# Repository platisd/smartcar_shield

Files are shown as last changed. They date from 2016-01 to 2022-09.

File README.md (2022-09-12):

# Smartcar shield








A versatile and easy to use vehicle platform for hobby-grade projects

- [Description](#description)
- [Hardware](#hardware)
- [Software](#software)
- [Reference platforms](#reference-platforms)
- [How to get started](#how-to-get-started)
- [Dependencies](#dependencies)
- [Project documentation](#project-documentation)
- [License](#license)

## Description
This repository, includes everything necessary to set up a Smartcar platform.
The Smartcar, is a vehicular educational platform, which enables the user to develop
various robotic applications in an affordable, pedagogic and easy way. It is intended
for persons with basic programming knowledge and little to no experience of electronics,
mechanics or robotics. More experienced users, should also find this approach convenient,
due to its open source nature, high level API and object oriented design.

## Hardware
Despite the software being hardware-agnostic, historically, development has been based on specific
hardware. Initially, the **Smartcar shield** was used on top of an Arduino, using cheap car kits.
This setup will be referred to as `shield` or `v1`.

Since the winter of 2019, a new platform was developed from scratch, using the WiFi and Bluetooth
enabled ESP32 as the vehicle's "brain". This setup will be referred to as `platform` or `v2` and
will be considered the default one from now on. It offers greater robustness and many more
possibilities, as it offers out-of-the-box connectivity.

### Platform

smartcar platform

The Smartcar platform is a complete hardware solution for your hobby-grade, connected vehicle project.
It is comprised of the chassis, made out of printed circuit boards, stacked on each other and an
ESP32 development board that drives the motors, controls the sensors and communicates with the
world via WiFi and Bluetooth.

There are 4 motors with directional odometers which enable not only to determine how much the
wheels have moved but also the direction they spin. It is equipped with a GY-50 gyroscope module
(based on the L3G4200D sensor) to provide heading information and sockets to optionally connect
4 `VL45L0X` LIDAR sensors to provide distance measurements. It is powered up by 8 AA batteries
and you can find the boards' source files in [extras/eagle/smartcar_platform](/extras/eagle/smartcar_shield).

### Shield

smartcar_shield

The Smartcar shield is an open hardware PCB, that is effortlessly stacked on top of an Arduino. It
includes an L293D H-bridge chip, that drives the motors, screw terminals to connect the motors
and a battery to them and a GY-50 gyroscope module (based on the L3G4200D sensor).
In [extras/eagle/smartcar_shield](/extras/eagle/smartcar_shield) you can find the
design files for the board, in a modifiable form, using free software. There are
also the options, to order it as-is, from either USA or China based manufacturers.

The Smartcar shield, facilitates efficient cable management, helps to preserve space
and is as small as possible, in order to keep the manufacturing price low. Additionally,
the components necessary to assemble it, are widely available over the Internet. Furthermore,
you can find 2D CAD drawings of the Smartcar chassis in various formats, at
[/extras/cad/2D](extras/cad/2D) which you can freely use in order to fabricate your own,
e.g. with a milling machine or a laser cutter.

### Emulator

[SMCE](https://github.com/ItJustWorksTM/smce-gd/) is the digital twin of the Smartcar platform
along with a cool and customisable 3D world for your rover to roam in.<br>
The core concept is that you write Arduino code that runs on both the real hardware as well as
the virtual environment.
This way, the need to have exclusive and frequent access to the car can be either alleviated
or drastically decreased.
The emulator allows limiting the unavoidable engagement with the physical car, to the point a
team of developers may develop their features on the emulator and only access the real hardware
to verify them.

## Software
The software, is the Smartcar shield Arduino library. It sports a high level API, meant to
enable its users to perform tasks easily with relatively few lines of code. It intends to
hide implementation details or low level hardware operations. The library, handles
the various components (i.e. the vehicle and the various sensors) as objects, therefore
enabling trivial control over the car's functions. The various operations exposed by the API,
are thoroughly explained in [API Documentation](https://platisd.github.io/smartcar_shield/).
You can find examples on how to use the library, in [/examples](/examples).

The library is versatile and is independent from the shield or specific hardware.
Particularly, its most important feature is that it supports multiple ways of steering and
throttling with different types of motors. Moreover, it is possible to steer the vehicle by
rotating the wheels on each side at a different speed, like a tank as well as by using a
servo motor. Another option is to use a brushed DC motor for steering, a setup that is very
common in cheap RC cars. Additionally, apart of the default brushed DC motors that are
connected to the Smartcar shield, you can also use an electronic speed controller (ESC)
in order to drive (throttle) the vehicle, using the very same library.

If the Smartcar shield library is installed through the Library Manager of Arduino IDE, as
recommended, the user will receive a notification in their IDE, when new versions are released
making updates particularly easy, without the need to use GitHub or git.

## Reference platforms

### Smartcar platform (default setup)

* 1 x [Modules board (rev.2)](https://www.pcbway.com/project/shareproject/Smartcar___Modules_board_rev_2.html)
* 1 x [Motor board (rev. 0)](https://www.pcbway.com/project/shareproject/Smartcar___Motors_board.html)
* 4 x [Brushed motors](https://www.aliexpress.com/item/32872592243.html) (530rpm @ 12V)
* 2 x [TXS0108E TTL level shifters](https://www.aliexpress.com/item/32472491036.html)
* 1 x DOIT ESP32 devkit v1 (30 GPIO pins)
* 1 x [TB6612FNG dual motor driver (Sparkfun)](https://www.sparkfun.com/products/14451)
* 4 x M6 (30mm) screws
* 4 x M6 nuts
* 16 x M3 (10mm) screws
* 16 x M3 nuts
* 2 x [HSP 02052 Front Bumper](https://www.aliexpress.com/item/32753903115.html)
* 10 x 6pin 2.54 pitch female pin headers
* 2 x 15pin 2.54 pitch female pin headers
* 1 x GY-50 gyroscope
* 4 x [8pin 2.54 pitch long male pin headers](https://www.aliexpress.com/item/32911455899.html) (30mm long)
* 4 x 8pin 2.54 pitch female pin headers
* 3 x 10KOhm resistors
* 8 x [AA battery holders](https://www.electrokit.com/produkt/batterihallare-1xaa-pcb/)
* 1 x [DD40AJSA adjustable buck converter](https://www.aliexpress.com/item/32816584868.html)
* 1 x [SPDT switch](https://www.tme.eu/en/details/5ms1s102am2qe/slide-switches/)
* 4 x [VL45L0x ToF distance sensors](https://www.aliexpress.com/item/32828144370.html) (optional)
  * 4 x 4pin 2.54 angled headers to mount the sensors vertically

### Smartcar shield

 * Smartcar chassis
 * [Smartcar shield PCB](extras/eagle/smartcar_shield)
 * L293D H-bridge
 * GY-50 gyroscope module
 * Two odometers (speed encoders) ([[1]](http://www.aliexpress.com/item/5pcs-IR-Infrared-Slotted-Optical-Speed-Measuring-Sensor-Optocoupler-Module-For-Motor-Test-For-Arduino-PIC/32465670452.html)
 and [[2]](http://www.aliexpress.com/item/HC-020K-Double-Speed-Measuring-Sensor-Module-with-Photoelectric-Encoders-Kit-top/32453020060.html)
 will suit commercially available chassis.
 [[3]](http://www.aliexpress.com/item/Correlation-photoelectric-sensor-lot-Infrared-correlation-count-sensor-module/2038553959.html)
 require some slight modifications)
 * Male & female pin headers (optionally get stackable Arduino headers too)
 * Five 2-pin screw terminals
 * Pin jumper
 * DIP16 socket
 * 0.1uF capacitors (2)
 * 100uF capacitor
 * 9V or 12V battery pack (do not use a single 9V battery)

### Supported sensors
 * Distance sensors
    * Ultrasonic
      * HC-SR04
      * SRF08
    * Infrared
      * SHARP GP2D120
      * SHARP GP2Y0A02
      * SHARP GP2Y0A21
 * Gyroscopes
   * GY-50 (L3G4200D)
 * Odometers
   * Directional (4+ pins)
   * Non-directional (3-pins)

## How to get started
 * Assemble the vehicle
 * [Install the library](https://www.ardu-badge.com/Smartcar%20shield)
 * [Connect the motors appropriately](examples/Car/shieldMotorsTest/shieldMotorsTest.ino) (if using the shield)
 * [Getting started with the Smartcar Platform](https://www.hackster.io/platisd/getting-started-with-the-smartcar-platform-1648ad)

## Dependencies
All dependencies should be downloaded automatically by the Arduino IDE's library manager.

- [Wire library](http://arduino.cc/en/reference/Wire)
- [Servo library](https://www.arduino.cc/en/reference/servo)
- [ServoESP32](https://github.com/RoboticsBrno/ServoESP32)
- [ESP32 AnalogWrite](https://github.com/ERROPiX/ESP32_AnalogWrite)

## Project documentation
* [API Documentation](https://platisd.github.io/smartcar_shield/)
* [The Smartcar platform](http://plat.is/smartcar)
* [Wiki](https://github.com/platisd/smartcar_shield/wiki)
* [Turning software engineers into Makers](https://platis.solutions/blog/2016/06/17/turning-software-engineers-into-makers/)

## License
MIT

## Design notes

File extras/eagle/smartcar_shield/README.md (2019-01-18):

# Smartcar shield CAD files

### Description
Here you can find the files necessary in order to edit or manufacture the Smartcar shield PCB. The files can be opened using CAD software, such as Eagle PCB that is free for personal use and KiCad, which is open source. The .sch file includes the logical schematic of the circuit, that is how the various components are connected to each other and the .brd file illustrates how they will be printed on the actual board.

All components that are needed for the board, are through-hole, for easy soldering. Finally, feel free to edit or redistribute the shield. Pull requests are always welcome.

### Order a PCB
If you do not want to bother with CAD softwareand just want to buy the PCBs for the shield, I have uploaded the necessary files in two popular services, [OSH-Park](https://oshpark.com/) (USA) and [PCBWay](https://www.pcbway.com/) (China), so they can be purchased with a few clicks.

**Note: I am not affiliated with either of these services, however I do receive a 10% commission in coupons from [PCBway](https://www.pcbway.com/) when you order the boards from them.**

* [PCBWay](https://www.pcbway.com/project/shareproject/SmartCar_Shield_rev__2.html) (rev. 2)
* [OSH-Park](https://oshpark.com/shared_projects/pCO3kBPB) (rev. 2)

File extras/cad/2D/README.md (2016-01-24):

# 2D CAD files
You can use or edit these files, in order to fabricate your own Smartcar chassis.

### Formats
* *.dxf
* *.dwg

### Preview
smartcar chassis

### License
CC BY-SA 4.0

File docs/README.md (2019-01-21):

# Smartcar shield library documentation
Welcome to the Smartcar shield library. These pages are intended to provide information
on how to use the library's API with explanations and examples for every exposed method.

If you are viewing this as source code or as a single page on
[github.com](https://github.com/platisd/smartcar_shield),
please go to the dedicated documentation pages on
[github.io](https://platisd.github.io/smartcar_shield/). These pages are
automatically generated by [Doxygen](http://www.doxygen.nl) and
[Travis CI](https://travis-ci.org/) after every commit, meaning that they are
the most probable source of up-to-date documentation.

Click on the [Classes](https://platisd.github.io/smartcar_shield/annotated.html)
tab for documentation on the various classes and
[Files](https://platisd.github.io/smartcar_shield/files.html) for an overview of
the dependencies between the different packages.

## About the library
The library sports a high level API, meant to enable its users to perform tasks
easily with relatively few lines of code. It intends to hide implementation
details or low level hardware operations. The library, handles the various
components (i.e. the vehicle and the various sensors) as objects, therefore
enabling trivial control over the car's functions.

The examples are primarily tailored to be used with the
[Smartcar Shield](https://github.com/platisd/smartcar_shield/tree/master/extras/eagle/smartcar_shield)
which was the hardware initially coupled with this software. However, by using different
arguments the different classes can be reused with practically any Motor and Control
combination common to miniature vehicles. Additionally, a plethora of hobby-grade
sensors are supported which potentially makes this library the only external component
necessary for many robotic or autonomous driving use cases, when it comes to
programming the microcontroller.

## Extending the library
All classes implement an interface which allow you to create library extensions
and give you the possibility of writing code that can be reused among different
platforms and hardware setups. Furthermore, despite the library written for
Arduino-compatible microcontrollers, potentially any microcontroller could be used
by providing your own implementation of the Runtime interface.

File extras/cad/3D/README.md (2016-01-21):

# 3D CAD files
You can use or edit these files, in order to generate your own 3D models of the Smartcar. The files are not hosted in the GitHub repository, due to their large size.

### Formats
* *.FCStd (FreeCAD)

### Downloads
* [smartcar.FCStd](https://www.dropbox.com/s/5tlktj8q3xssbsc/smartcar.FCStd?dl=1) by Pablo Avendaño, Pablo Pérez and Andrés Flores from Universidad Adventista del Plata, Argentina

3D render

### License
CC BY-SA 4.0

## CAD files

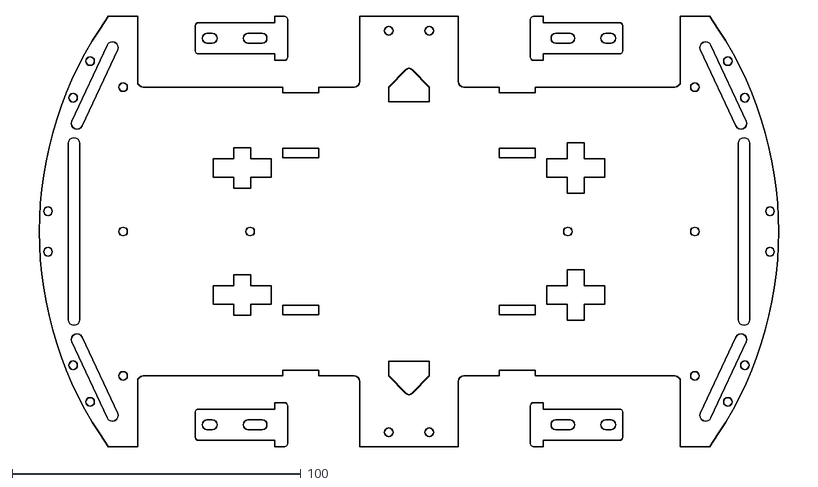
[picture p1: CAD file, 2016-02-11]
extras/cad/2D/SmartCar_chassis_NoAxesDimensions.dxf
271.9 x 149.0

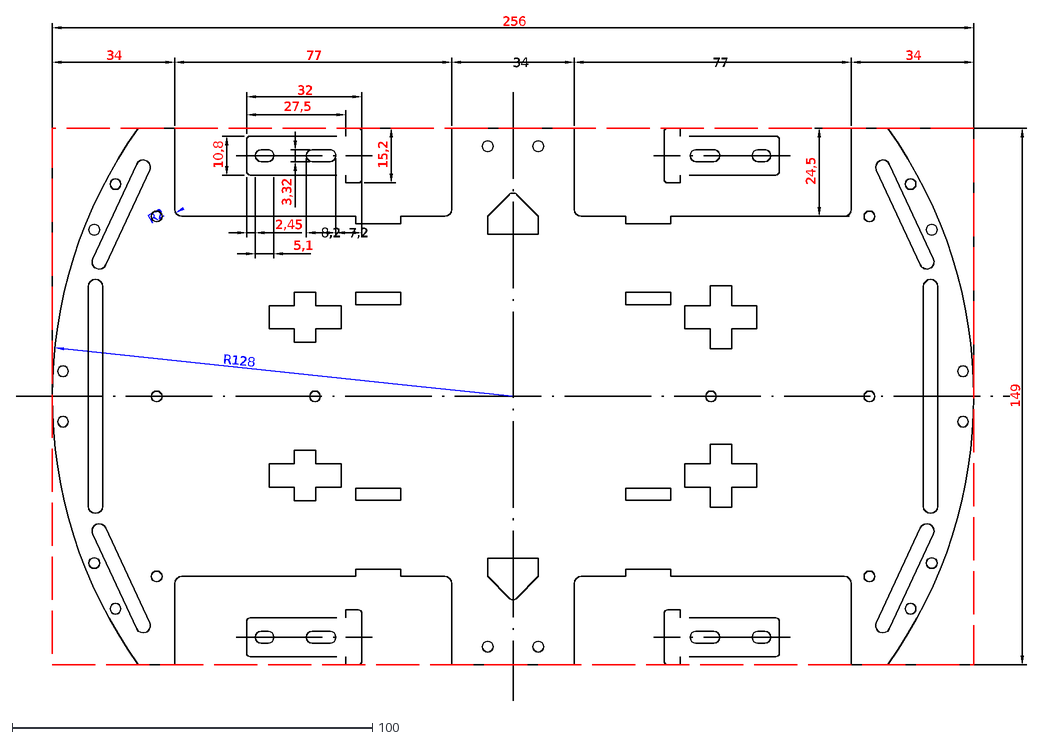
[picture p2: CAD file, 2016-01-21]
extras/cad/2D/SmartCar_chassis.dxf
77
34
149
24,5
R128
R2
256
32
27,5
10,8
15,2
3,32
2,45
8,2
7,2
5,1

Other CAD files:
extras/cad/2D/SmartCar_chassis.dwg

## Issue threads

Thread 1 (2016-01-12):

Add support for MPU-6050

DouglasPearless, 2016-01-12:
Would you be able to add support for the MPU-6050 board ( GY-521 gyroscope module ) in addition to the existing MPU-3050 (GY-50 gyroscope module)?

Cheers
Douglas

DouglasPearless, 2016-01-12:
Hmm, re-reading the documentation is that it appears that L3G4200D is the supported chip not MPU-3050, any way, would you be able to add MPU-6050 support?

platisd, 2016-01-12:
Hi, I have an MPU-6050 module lying somewhere around and it's been a while since I used it (2.5 years to be exact!).

Are you interested in just software support or hardware as well, on the shield?

If it's the former, then I might be able to do something, as I want to steadily decouple the library from the hardware shield. Currently I am adding support for steering with a servo and throttling using an ESC. This is expected to be done in the next two weeks. Afterwards, I could add the MPU-6050 since it's a fairly popular component. If you have any piece of code that works well with it, you can let me know so I can use it as a reference and hopefully finish the new feature faster.

However if you are talking about hardware support on the shield, I cannot promise that I will do it, as it is a big change and I need to be convinced first that it's better than the existing approach. Of course, you are always welcome to create a fork of the shield that has slots for MPU-6050! :)

DouglasPearless, 2016-01-12:
Hi Dimitris,

Just the software support, please.

I have seen some Arduino code for it and I will see if I can find it again.

Servo steering and ESC will be interesting, but for the moment I am using two DC motors with gearboxes to drive my robot.

Will need to add a compass too!

Cheers
Douglas

Sent from my iPhone

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

platisd, 2016-01-12:
Cool, will do after I am done with the other stuff that are currently being done!

Regarding the compass, the problem with the (cheap) compasses, according to my experience, is that they pick a lot of interference, becoming unstable and therefore they will not necessarily work out of the box. This will ruin the user experience, possibly leading novice users to frustration. :P
Therefore I don't think it makes sense to add a Compass class for example in the library, for the time being.

DouglasPearless, 2016-01-12:
Here is a link to a good (IMHO) tutorial on using the MPU-6050 http://diyhacking.com/arduino-mpu-6050-imu-sensor-tutorial/ <http://diyhacking.com/arduino-mpu-6050-imu-sensor-tutorial/>
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

platisd, 2016-01-12:
I'll give it a look when the time comes and will let you know when the new feature will be added, thanks!

DouglasPearless, 2016-01-12:
Thanks, I look forward to trying the code :-)

platisd, 2016-01-29:
Hello again @DouglasPearless ,

I present you with the [Smartcar MPU6050](https://github.com/platisd/smartcar_MPU6050) library. It is an extension of the Smartcar shield library, for the MPU6050, which is essentially a stripped down version of the [MPU6050 Arduino library](https://github.com/jrowberg/i2cdevlib/tree/master/Arduino/MPU6050), by Jeff Rowberg. I did not include it in this, "core" library, because it is rather... extensive. So, if someone wants to use it, will have to include that specific header file.

Furthermore, it can be used by the smartcar, the same way as the Gyroscope, namely, it can be utilized to make the car [rotate](../wiki/API-documentation#void-rotateint-degrees). You can also `getAngularDisplacement()`, as you did with the [Gyroscope](../wiki/API-documentation#int-getangulardisplacement).

You will find further documentation and examples in the Smartcar MPU6050 library's [readme](https://github.com/platisd/smartcar_MPU6050/blob/master/README.md).

There are some known issues, however aside of that it should be working very well most of the time. If you have problems with it, open an issue in the other library. :)

DouglasPearless, 2016-01-30:
Great, I will have a look at it in a while.

Closed 2016-01-29.

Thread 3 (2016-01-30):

getSpeed and GetDirection

DouglasPearless, 2016-01-30:
As there are DCMotors::setSpeed and DCMotors::setAngle methods, would it be possible to have DCMotors::getSpeed and DCMotors::getAngle methods as well to enable the code to determine where the robot is heading?

Cheers
Douglas

platisd, 2016-01-30:
Hi,

They actually have those methods, which are implemented in the parent classes. The DCMotors class extends the SteeringMotor class as well as the ThrottleMotor class (since in some cases you use them for both steering and throttling).

Therefore, you can getAngle and getSpeed from them. However, I would advise against using the DCMotors class directly in your sketches. There is a reason there is no example using any kind of Motor class directly. :P
This is because the Car class abstracts everything motor related, so you can use the same code, regardless of the motors you have on your vehicle. (E.g. you could be using a servo for steering and a motor connected with an ESC for throttling or a servo for steering and DC motor for throttling or even just DC motors for steering and throttling). The code should be essentially the same across all those settings. That is why the Car class is there, so the user deals with it and not with the different motors on each occasion. :)

To sum up, if the user wants to getSpeed or getAngle, he should talk to the Car and not the motors, as the motors could vary depending on your setting. Please refer to the [API documentation] (https://github.com/platisd/smartcar_shield/wiki/API-documentation) regarding the usage of the various library components.

Last but not least, getSpeed and getAngle in any case, will NOT give you the "actual speed" of the car or the "actual angle" (I.e. heading). If you used setSpeed(50), then getSpeed will return 50. If you wrote setAngle(0), then getAngle will merely return 0, not the actual heading of the car.

If you want to get the actual speed in meters per second, you should talk to the Odometers (encoder). As they can actually measure distance (and therefore speed), you can use their getSpeed method to get "the ground speed" in meters per second. If you want to get a heading, then you will have to rely on a HeadingSensor (I.e. a gyroscope or the newly added MPU6050).

I am closing this issue, as I believe the features that are requested are already there! :)

DouglasPearless, 2016-01-30:
Thanks for the comprehensive feedback!

platisd, 2016-01-30:
You're welcome! I am eager to see how you will use this library! :)

DouglasPearless, 2016-01-30:
The first thing I need to solve is the two DC drive motors run at different speeds and how I can get the car to drive in a straight line.

platisd, 2016-01-30:
Hehe, that can be a very complicated task, the complexity of which increases along with the extent/accuracy of how straight you want it to go. I have some ideas, but if you don't mind, let's continue this discussion elsewhere! You can reach me at dimitris@plat.is :)

Closed 2016-01-30.

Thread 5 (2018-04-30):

Cruise control suffers from runaway due to temporary sensor failure

michalpalka, 2018-04-30:
The cruise control functionality of the library can cause runaway as a result of a temporary sensor failure. As a consequence, the controlled rover moves in the direction opposite to the requested one at maximum speed.

The problem affects the cruise control functionality enabled using `car.enableCruiseControl()`. We observed it with [this rover type](https://platis.solutions/blog/2016/06/17/turning-software-engineers-into-makers/).

The problem manifests when the rover is commanded to drive forward, but is still standing and the odometers temporarily report high moving speed due to signal transmission failure. The controller will then apply negative torque (meant for braking), which accelerates the rover backwards. As the rover accelerates backwards, the odometers correctly report increasing speed (the odometers report the absolute speed, not the direction), which is interpreted as the rover moving forward too fast. This results in more negative torque being applied, and a complete runaway with the rover racing backwards.

The following sketch can be used to demonstrate the problem.

```
#include <Smartcar.h>

Odometer encoderLeft(188), encoderRight(188);
Gyroscope gyro(22);
Car car;

const int encoderLeftPin = 2;
const int encoderRightPin = 3;
const float fSpeed = 0.3; //a ground speed (m/sec) for going forward
bool sw = false;

void setup() {
  Serial3.begin(9600);
  encoderLeft.attach(encoderLeftPin);
  encoderRight.attach(encoderRightPin);
  gyro.attach();
  delay(1500);
  gyro.begin(60);
  encoderLeft.begin();
  encoderRight.begin();
  car.begin(encoderLeft, encoderRight, gyro); //initialize the car using the encoders
  car.enableCruiseControl(); //using default PID values
  car.setAngle(0);
 // car.enableCruiseControl(12,5,17,30); //using custom values and control frequency
  car.setSpeed(fSpeed);
}

void loop() {
  car.updateMotors();
  handleInput();
}

int state = 0;

void handleInput() {
  int t = millis();
  if (t >= 1000 && state < 1) {
    car.setSpeed(fSpeed);
    state = 1;
  } else if (t >= 3000 && state < 2) {
    car.setSpeed(0);
    state = 2;
  }

}
```

The sketch uses the cruise control functionality, requesting to drive forward at 1 s after setup, and then stopping at 3 s. The correct behaviour with the sketch is the rover driving forward and then stopping.

We managed to trigger erroneous behaviour by using the rover with depleted batteries. With that setup, the rover will occasionally race backwards instead of moving forward. We observed incorrect behaviour once every 4 attempts or so, but this probability is greatly dependent on the state of the batteries. We also observed it by using an incomplete battery pack (6 1.5 V batteries instead of 8), giving the measured voltage 8.4 V dropping to 6.4 V under load (we could not measure voltage under load reliably due to how fast was changing). Connecting the Arduino board to USB power makes the problem go away completely.

We traced the problems to the odometers returning high speeds temporarily when the rover is standing or moving slowly. We don’t know what causes the incorrect readouts. We suspect that the voltage ripple from the motor controller is interpreted as signal edges from the odometers.

We believe that the cause of the incorrect readouts should be investigated, but the fundamental problem here is that the control turns a small disturbance (or input corruption) into a complete runaway. Using odometers that also report the direction of movement in addition to the speed would solve the problem. With the current odometers, the controller should be somehow constrained to avoid the runaway.

michalpalka, 2018-04-30:
@platisd @Shaun-McMurray @guslauer @ArchiCo @FFrostYY

platisd, 2018-05-02:
I will start looking into this. I think the problem that needs to be investigated is whether there are ways to safeguard against faulty odometer readings however these may occur.

As you correctly mentioned, the "simple" Odometers cannot determine direction of movement and that is why some "special" logic is in place when it comes to stopping or changing direction of movement. Specifically, when the vehicle is driving forward and we command it to start going backward, from an odometer perspective there is no difference between these two states. That's why we try to [stop](https://github.com/platisd/smartcar_shield/blob/master/src/Car.cpp#L100) the car first by applying some torque in the opposite direction

To accelerate in the investigation, it would be great to provide some logs, i.e. the speed of the car (`Car::getSpeed()`) and the current state. Since the problem is not observed when the board is connected via USB, you should use a Bluetooth module or any other wireless means of communication.

guslauer, 2018-05-05:
Reverse:
Car speed | Right odometer speed | Left odometer speed | Battery pack voltage
--- | --- | --- | ---
0.35 | 0.11 | 0.38 | 9.59
0.35 | 0.11 | 0.38 | 9.59
0.35 | 0.11 | 0.38 | 9.52
0.35 | 0.11 | 0.38 | 9.59
0.35 | 0.11 | 0.38 | 9.57
0.35 | 0.11 | 0.38 | 9.57
0.35 | 0.11 | 0.38 | 9.52
0.35 | 0.11 | 0.38 | 9.57
0.35 | 0.11 | 0.38 | 9.57
0.35 | 0.11 | 0.38 | 9.55
0.35 | 0.11 | 0.38 | 9.57
0.35 | 0.11 | 0.38 | 9.55
0.35 | 0.11 | 0.38 | 9.57
0.35 | 0.11 | 0.38 | 9.57
0.35 | 0.11 | 0.38 | 9.47
0.35 | 0.11 | 0.38 | 8.33
0.35 | 0.11 | 0.38 | 9.30
0.35 | 0.11 | 0.38 | 9.50
0.35 | 0.11 | 0.38 | 9.47
0.35 | 0.11 | 0.38 | 9.47
0.35 | 0.11 | 0.38 | 9.47
0.35 | 0.11 | 0.38 | 9.47
0.35 | 0.11 | 0.38 | 9.47
0.35 | 0.11 | 0.38 | 8.98
0.35 | 0.11 | 0.38 | 9.45
0.35 | 0.11 | 0.38 | 8.01
0.35 | 0.11 | 0.38 | 9.38
0.35 | 0.11 | 0.38 | 9.13
0.35 | 0.11 | 0.38 | 9.30
0.35 | 0.11 | 0.38 | 9.40
0.35 | 0.11 | 0.38 | 9.35
0.35 | 0.11 | 0.38 | 9.38
0.35 | 0.11 | 0.38 | 7.52
0.35 | 0.11 | 0.38 | 9.38
0.35 | 0.11 | 0.38 | 9.35
0.35 | 0.11 | 0.38 | 9.13
0.35 | 0.11 | 0.38 | 6.69
0.35 | 0.11 | 0.38 | 8.76
0.35 | 0.11 | 0.38 | 9.25
0.35 | 0.11 | 0.38 | 9.13
0.35 | 0.11 | 0.38 | 9.20
0.35 | 0.11 | 0.38 | 9.01
0.35 | 0.11 | 0.38 | 9.23
0.35 | 0.11 | 0.38 | 9.25
0.35 | 0.11 | 0.38 | 8.45
0.35 | 0.11 | 0.38 | 7.69
0.35 | 0.11 | 0.38 | 6.49
0.35 | 0.11 | 0.38 | 9.13
0.35 | 0.11 | 0.38 | 8.69
0.35 | 0.11 | 0.38 | 8.96
0.35 | 3.34 | 0.38 | 9.16
0.35 | 3.34 | 0.38 | 9.08
0.35 | 3.34 | 0.38 | 9.13
0.35 | 3.34 | 0.38 | 9.25
0.35 | 3.34 | 0.38 | 9.42
0.35 | 3.34 | 0.38 | 9.45
0.35 | 3.34 | 0.38 | 9.38
0.35 | 3.34 | 0.38 | 9.13
0.35 | 3.34 | 0.38 | 9.33
0.35 | 3.34 | 0.38 | 9.25
0.35 | 3.34 | 0.38 | 9.16
0.35 | 3.34 | 0.38 | 9.20
0.35 | 3.34 | 0.38 | 6.93
0.35 | 3.34 | 0.38 | 9.01
0.35 | 0.01 | 0.38 | 8.47
0.35 | 0.01 | 0.38 | 8.74
0.35 | 0.01 | 0.00 | 7.15
0.35 | 0.06 | 0.16 | 8.03
0.35 | 0.06 | 0.16 | 9.20
0.35 | 0.10 | 0.09 | 9.08
0.35 | 0.10 | 0.16 | 9.20
0.35 | 0.07 | 0.16 | 9.30
0.35 | 0.07 | 0.09 | 9.28
0.35 | 0.10 | 0.09 | 9.30
0.35 | 0.10 | 0.14 | 8.98
0.35 | 0.10 | 0.14 | 9.38
0.35 | 0.10 | 0.07 | 7.84
0.35 | 0.05 | 0.07 | 9.40
0.35 | 0.05 | 0.07 | 9.33
0.35 | 0.05 | 0.07 | 9.40
0.35 | 0.05 | 0.07 | 9.45
0.35 | 0.05 | 0.07 | 9.47
0.35 | 0.05 | 0.07 | 9.47
0.35 | 0.05 | 0.07 | 9.38
0.35 | 0.05 | 0.07 | 9.47
0.35 | 0.05 | 0.07 | 9.50
0.35 | 0.05 | 0.07 | 9.45
0.35 | 0.05 | 0.07 | 9.23
0.35 | 0.05 | 0.07 | 9.40
0.35 | 0.05 | 0.07 | 9.45
0.35 | 0.05 | 0.07 | 9.38
0.35 | 0.05 | 0.07 | 9.42
0.35 | 0.05 | 0.07 | 9.35
0.35 | 0.05 | 0.07 | 9.35
0.35 | 0.05 | 0.07 | 9.38
0.35 | 0.05 | 0.07 | 8.79
0.35 | 0.05 | 0.07 | 8.28
0.35 | 0.05 | 0.07 | 6.71
0.00 | 0.05 | 0.07 | 9.18
0.00 | 0.05 | 0.07 | 9.42
0.00 | 0.05 | 0.07 | 9.45
0.00 | 0.05 | 0.07 | 9.50
0.00 | 0.05 | 0.07 | 9.50
0.00 | 0.05 | 0.07 | 9.50
0.00 | 0.05 | 0.07 | 9.52
0.00 | 0.05 | 0.07 | 9.52
0.00 | 0.05 | 0.07 | 9.52

Not moving:

guslauer, 2018-05-05:
# Logs
Here are some logs from today's troubleshooting session with @Shaun-McMurray. We tried to replicate the reversing behavior with the battery pack having different voltages, and it was, as previously mentioned, very apparent that this reversing behavior happened more often when the voltage was low. The logs were sent over Bluetooth, thus no USB cable was connected to the car during the testing.

The car speed was retrieved by `Car::getSpeed()`, odometer speed by `odometer::getSpeed()` and the 'battery pack voltage' from a voltage divider connected to the battery pack and to an analog pin on the Arduino.

In addition to the reversing behavior of the car, we also observed that the car did not move at all at times. See the section at the bottom for logs retrieved when that happened.

#### Normal behavior (control):
Car speed | Right odometer speed | Left odometer speed | Battery pack voltage
--- | --- | --- | ---
0.40 | 0.11 | 0.10 | 9.64
0.40 | 0.11 | 0.10 | 9.38
0.40 | 0.11 | 0.10 | 9.45
0.40 | 0.11 | 0.10 | 9.64
0.40 | 0.11 | 0.10 | 9.64
0.40 | 0.11 | 0.10 | 9.50
0.40 | 0.11 | 0.10 | 8.96
0.40 | 0.11 | 0.10 | 9.30
0.40 | 0.11 | 0.10 | 9.45
0.40 | 0.11 | 0.10 | 9.38
0.40 | 0.11 | 0.10 | 9.42
0.40 | 0.11 | 0.10 | 9.42
0.40 | 0.11 | 0.10 | 9.40
0.40 | 0.11 | 0.10 | 9.40
0.40 | 0.11 | 0.10 | 8.47
0.40 | 0.11 | 0.10 | 8.28
0.40 | 0.11 | 0.10 | 6.71
0.40 | 0.11 | 0.10 | 9.08
0.40 | 0.11 | 0.10 | 8.54
0.40 | 0.11 | 0.10 | 8.91
0.40 | 0.11 | 0.10 | 9.13
0.40 | 0.11 | 0.10 | 8.98
0.40 | 0.11 | 0.00 | 9.06
0.40 | 0.11 | 0.00 | 6.10
0.40 | 0.11 | 0.08 | 8.86
0.40 | 0.00 | 0.22 | 7.20
0.40 | 0.00 | 0.13 | 8.45
0.40 | 0.00 | 0.26 | 6.13
0.40 | 0.07 | 0.16 | 7.69
0.40 | 0.07 | 0.30 | 8.86
0.40 | 0.09 | 0.36 | 8.54
0.40 | 0.19 | 0.21 | 8.76
0.40 | 0.14 | 0.24 | 6.86
0.40 | 0.26 | 0.26 | 8.86
0.40 | 0.29 | 0.28 | 8.08
0.40 | 0.20 | 0.29 | 6.81
0.40 | 0.33 | 0.30 | 6.67
0.40 | 0.37 | 0.32 | 6.62
0.40 | 0.36 | 0.58 | 8.69
0.40 | 0.39 | 0.57 | 7.84
0.40 | 0.28 | 0.60 | 8.47
0.40 | 0.27 | 0.34 | 7.96
0.40 | 0.27 | 0.35 | 8.76
0.40 | 0.28 | 0.61 | 8.86
0.40 | 0.28 | 0.62 | 6.57
0.40 | 0.30 | 0.61 | 7.45
0.40 | 0.30 | 0.36 | 6.79
0.40 | 0.30 | 0.65 | 8.47
0.40 | 0.31 | 0.66 | 6.64
0.40 | 0.33 | 0.37 | 7.93
0.40 | 0.47 | 0.65 | 8.84
0.40 | 0.52 | 0.65 | 8.62
0.40 | 0.49 | 0.36 | 8.76
0.40 | 0.51 | 0.65 | 6.96
0.40 | 0.52 | 0.67 | 8.62
0.40 | 0.51 | 0.38 | 7.45
0.40 | 0.33 | 0.70 | 7.98
0.40 | 0.34 | 0.36 | 6.81
0.40 | 0.34 | 0.68 | 6.76
0.40 | 0.50 | 0.69 | 8.79
0.40 | 0.55 | 0.38 | 8.35
0.40 | 0.54 | 0.70 | 8.67
0.40 | 0.34 | 0.70 | 7.69
0.40 | 0.35 | 0.39 | 8.86
0.40 | 0.58 | 0.64 | 8.91
0.40 | 0.53 | 0.67 | 6.79
0.40 | 0.48 | 0.35 | 7.37
0.40 | 0.48 | 0.64 | 6.88
0.40 | 0.49 | 0.61 | 8.79
0.40 | 0.31 | 0.35 | 7.93
0.40 | 0.30 | 0.35 | 8.57
0.40 | 0.30 | 0.59 | 8.94
0.40 | 0.30 | 0.59 | 8.81
0.40 | 0.31 | 0.57 | 8.89
0.40 | 0.29 | 0.33 | 6.81
0.40 | 0.29 | 0.32 | 8.67
0.40 | 0.29 | 0.60 | 7.32
0.40 | 0.29 | 0.59 | 8.57
0.40 | 0.29 | 0.59 | 6.69
0.40 | 0.28 | 0.59 | 7.91
0.40 | 0.29 | 0.33 | 8.89
0.40 | 0.30 | 0.34 | 8.69
0.40 | 0.30 | 0.54 | 8.84
0.40 | 0.29 | 0.59 | 7.45
0.40 | 0.28 | 0.55 | 8.89
0.40 | 0.28 | 0.54 | 8.62
0.40 | 0.41 | 0.54 | 8.01
0.40 | 0.40 | 0.31 | 7.06
0.40 | 0.42 | 0.31 | 6.67
0.40 | 0.45 | 0.32 | 8.81
0.40 | 0.40 | 0.54 | 8.33
0.40 | 0.42 | 0.53 | 8.69
0.40 | 0.44 | 0.55 | 8.76
0.40 | 0.43 | 0.54 | 8.84
0.40 | 0.41 | 0.57 | 8.89
0.40 | 0.27 | 0.56 | 6.62
0.40 | 0.26 | 0.52 | 8.11
0.40 | 0.25 | 0.50 | 7.01
0.00 | 0.02 | 0.24 | 8.81
0.00 | 0.02 | 0.22 | 9.33

## Car reversing
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

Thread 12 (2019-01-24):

CI build is broken due to esp8266 package.json missing

platisd, 2019-01-24:
## Description
At the moment, the [esp8266 package](http://arduino.esp8266.com/stable/package_esp8266com_index.json) is not available which causes the [build](https://travis-ci.org/platisd/smartcar_shield/builds/484062841) to fail as it cannot compile the examples against the `esp8266` board.

## Definition of Done
* Retrigger the build once esp8266/Arduino#5664 is fixed or the website comes back up.

platisd, 2019-01-24:
Package source is online again so [build #187](https://travis-ci.org/platisd/smartcar_shield/builds/484062841) passed.

Closed 2019-01-24.

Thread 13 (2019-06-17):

Refactor 6 lines occurring 2 times in SRF08.cpp

platisd, 2019-06-17:
I've selected for refactoring 6 lines of code which are duplicated in 1 file(s) ([1](https://github.com/platisd/smartcar_shield/blob/9f7cde6211136f9c14b78415c428b739684f3e99/src/sensors/distance/ultrasound/i2c/SRF08.cpp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), [2](https://github.com/platisd/smartcar_shield/blob/9f7cde6211136f9c14b78415c428b739684f3e99/src/sensors/distance/ultrasound/i2c/SRF08.cpp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)).  Addressing this will make our codebase more maintainable and improve [Better Code Hub](https://bettercodehub.com)'s **Write Code Once** guideline rating! 👍

Here's the gist of this guideline:
- **Definition** 📖
Do not copy code.
- **Why**❓
When code is copied, bugs need to be fixed in multiple places. This is both inefficient and a source of regression bugs.
- **How** 🔧
Avoid duplication by never copy/pasting blocks of code and reduce duplication by extracting shared code, either to a new unit or introduce a superclass if the language permits.

You can find more info about this guideline in [Building Maintainable Software](http://shop.oreilly.com/product/0636920049159.do). 📖

----
ℹ️ To know how many _other_ refactoring candidates need addressing to get a guideline compliant, select some by clicking on the 🔲  next to them. The risk profile below the candidates signals (✅) when it's enough! 🏁

----
Good luck and happy coding! :shipit: :sparkles: :100:

Closed 2019-06-17.

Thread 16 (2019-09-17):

Remove unintended Arduino dependencies from Runtime interface

platisd, 2019-09-17:
## Description
The `Runtime` interface is supposed to be a platform agnostic representation of the
runtime environment.
Instead of passing arbitrary numbers (which will only work for Arduino), we should
instead pass generic enums and let each implementation determine how these
enums should be interpreted.

## Definition of Done
* Platform specific dependencies are removed

AeroStun, 2020-03-17:
While trying to add an ISP-EDF Runtime for this library (instead of forcing the Arduino one to be used), I've run into the `Servo` library being a runtime environment boundary; right now I can just conditionally polyfill it, but I was wondering if maybe you would rather simply abstract it away behind `Runtime`?

platisd, 2020-03-17:
For me, the biggest problem begins with the fact that we use inheritance instead of composition for the sake of simplicity.

```cpp
class ServoMotor : public Servo, public Motor
{
....
};
```

But anyway, I should probably not rant about unrelated stuff... :laughing:
I don't know if I understood your suggestion correctly, but I don't think that `Servo` should be part of the `Runtime` interface as it is typically a separate library. How/Where are you getting stuck exactly?

The Smartcar library is dependent on some kind of Servo library. On most Arduino microcontrollers, this is the [Servo](https://www.arduino.cc/en/reference/servo) library that comes with the IDE and for ESP32 is the [ServoESP32](https://github.com/RoboticsBrno/ServoESP32) one.

AeroStun, 2020-03-17:
Let's not ask me for suggestions on that first class problem else I'll end up proposing CRTP...

Well I am not using the Arduino Framework **at all**, which rules out that ServoESP32 library if I read its contents correctly (i.e. its PlatformIO config says that it only supports the Arduino Framework).

platisd, 2020-03-17:
> Let's not ask me for suggestions on that first class problem else I'll end up proposing CRTP...

:laughing:

> Well I am not using the Arduino Framework at all,

Cool, looking forward to see where this ends up.
From the top of my head the most straight forward way I see, is to create a `Servo.h` header available in the path and have a `Servo` implementation that provides the functionality in a similar API, i.e. with the `Servo::attach` and `Servo::writeMicroseconds` functions.

Thinking it twice, if we consider the "Servo functionality" as part of "Runtime" how would you propose we have it be considering that we need an instance of a "Servo" to have it working on Arduino?

AeroStun, 2020-03-17:
That's exactly what I have right now: a polyfill for the two functions currently used by the library

If we chose to put the Servo stuff in the Runtime abstraction, given the need of a separate instance, a Servo factory as a method of `Runtime` could be a feasible solution.
Otherwise we simply make it a separate point of customization with an abstract base class like the rest of your design (you really gotta love the devirtualizer don't you?)

platisd, 2020-03-17:
So what you propose is something like this (more or less pseudocode):

```cpp
struct BasicServo {
    virtual void writeMicroseconds() = 0;
    virtual void attach(pin) = 0;
};

struct Runtime {
    virtual BasicServo* getServo() = 0;
};

struct ServoMotor : public Motor {
    ServoMotor(Runtime& runtime) : mServo{runtime.getServo} {}

private:
    BasicServo* mServo;
};
```

And where in the `ArduinoRuntime` we would return a `Servo`, in `EspIdfRuntime` we would return a whatever the implementation is called?
I could consider it, especially since it will give as a single differentiation point, i.e. the Runtime, but will it make things otherwise easier?

AeroStun, 2020-03-17:
Correct; that does cause the problem of ownership however (i.e. how does `ServoMotor` know how to correctly handle `mServo` on destruction?)
It does however allow one to use the library on any runtime with any `Servo` implementation that they want

platisd, 2020-03-17:
Well, should we really care about destructing the servo instances? To me it does not _physically_ make sense, considering the application domain we are in. In other words, if there is a Servo it is always there and so is "the runtime".

> Applying the same treatment to BasicServo as there is already to all other devices (i.e. the user passes in a ref to an child class instance) might have the added benefit of allowing user-customization of the Servo implementation without messing with the Runtime

Sure, that would be even better and more consistent design-wise, however, what would the benefit be with regards to the effort and in the number of differentiation points?
In both cases one would need to create a `Servo` implementation and there would be two context/classes to change/differentiate when migrating to a new platform.

AeroStun, 2020-03-17:
> In other words, if there is a Servo it is always there and so is "the runtime". As I see it, these classes don't get destructed.
If you only ever have a fixed number of servos, that'll definitely do; if not, well, you do have to release them. Note that the Arduino-provided `<Servo.h>` gives a `MAX_SERVOS`, but the ESP32 one you previously linked does not.

 > [...] what would the benefit be with regards to the effort and in the number of differentiation points?
> In both cases one would need to create a Servo implementation and there would be two context/classes to change/differentiate when migrating to a new platform.
My point is that there is no difference in effort but one design allows direct user customization and the other simply doesn't so easily.

platisd, 2020-03-17:
> My point is that there is no difference in effort but one design allows direct user customization and the other simply doesn't so easily.

Then we are back to my initial rant then on preferring inheritance over composition. This was done to make it easier to use and because I could not find a good name for the `BasicServo` that would make sense. Perhaps a naming scheme such as `ArduinoServo`, `Esp32Servo` etc wouldn't be that bad and would even allow for a user to provide their own implementation without changing the library. Here I should note that having users provide their own types is not a common use-case for the current users of the library (i.e. university students) but perhaps as time passes it will become?

AeroStun, 2020-03-17:
I'll keep this conclusion in mind and will adapt my current polyfilling. I'll get back to you once I'll have managed to successfully write my runtime impl if you're interested in the possible results.

> Here I should note that having users provide their own types is not a common use-case for the current users of the library (i.e. university students) but perhaps as time passes it will become?

Well, your university students already use the ArduinoRuntime because it is a default parameter everywhere; I'd assume that Servo should get the same treatment and have `ArduinoServo` be an implicit default

platisd, 2020-03-17:
> Well, your university students already use the ArduinoRuntime because it is a default parameter everywhere; I'd assume that Servo should get the same treatment and have ArduinoServo be an implicit default

`ArduinoRuntime` as a default is honestly a hack that I am thinking of eventually getting rid of (maybe it's not that big of a deal to pass it around), but sure, that could be an idea! :smile:

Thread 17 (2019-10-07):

Refactor 11 lines occurring 2 times in DistanceCar.cpp

platisd, 2019-10-07:
I've selected for refactoring 11 lines of code which are duplicated in 1 file(s) ([1](https://github.com/platisd/smartcar_shield/blob/9efb83e6cfc651bccf523fc45b53ca06421a7307/src/car/distance/DistanceCar.cpp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), [2](https://github.com/platisd/smartcar_shield/blob/9efb83e6cfc651bccf523fc45b53ca06421a7307/src/car/distance/DistanceCar.cpp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)).  Addressing this will make our codebase more maintainable and improve [Better Code Hub](https://bettercodehub.com)'s **Write Code Once** guideline rating! 👍

Here's the gist of this guideline:
- **Definition** 📖
Do not copy code.
- **Why**❓
When code is copied, bugs need to be fixed in multiple places. This is both inefficient and a source of regression bugs.
- **How** 🔧
Avoid duplication by never copy/pasting blocks of code and reduce duplication by extracting shared code, either to a new unit or introduce a superclass if the language permits.

You can find more info about this guideline in [Building Maintainable Software](http://shop.oreilly.com/product/0636920049159.do). 📖

----
ℹ️ To know how many _other_ refactoring candidates need addressing to get a guideline compliant, select some by clicking on the 🔲  next to them. The risk profile below the candidates signals (✅) when it's enough! 🏁

----
Good luck and happy coding! :shipit: :sparkles: :100:

Closed 2020-02-10.

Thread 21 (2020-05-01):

Remove ArduinoRuntime hack

platisd, 2020-05-01:
## Description
Static instantiation of the `ArduinoRuntime` in `Smartcar.h` so it can be used as a conditional statement in different class constructors should be removed, as well as the default argument.

It seems that library users are starting off by copying the examples anyway, so it won't be too cumbersome.

## Definition of Done

* `Smartcar.h` does not instantiate an `ArduinoRuntime` instance, that is left for the user to do.
* Default runtime argument is removed from the constructors that use it.

platisd, 2020-05-01:
This will be done after the current iteration of DIT112 finishes to avoid disrupting the student projects.

Closed 2020-06-07.

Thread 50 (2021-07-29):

Fix code smells detected by Sonarqube

platisd, 2021-07-29:
## Description
Sonarqube has detected some code smells and the report can be found [here](https://sonarcloud.io/project/issues?id=platisd_smartcar_shield&resolved=false&types=CODE_SMELL).
Not all of them need to be fixed (i.e. ignore the ones about the commented-out code).

## Definition of Done
* Fix the code smells
* Find ways (if any) to avoid regressions (e.g. through `clang-tidy` or compiler warnings)

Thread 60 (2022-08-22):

support servo drivemotor?

samuk, 2022-08-22:
## Description
Does this lib support servos as drive motors?
## Definition of Done

This chassis works using just esp32 and 5v power source

https://m.aliexpress.com/item/32607362464.html

platisd, 2022-08-22:
At first I thought you meant an ESC ([which is supported](https://platisd.github.io/smartcar_shield/class_servo_motor.html)) but I now see that you mean those continuous rotation "servo" motors.

Can you remind me how do you set the speed for them? It shouldn't be hard to implement something if not already supported.

samuk, 2022-08-22:
it's just PWM https://dronebotworkshop.com/esp32-servo/

I think you already have the esp32servo lib installed?

platisd, 2022-08-22:
The particular sensors are a little special in the sense that you cannot set a "speed" on them. They just move at a set speed forward or backward. But anyway, if you replace `BrushedMotor` with `ServoMotor` in [SimpleCar.ino](https://github.com/platisd/smartcar_shield/blob/master/examples/Car/SimpleCar/SimpleCar.ino) it should work.

samuk, 2022-08-22:
Great I'll give it a go, thanks

Closed 2022-08-22.

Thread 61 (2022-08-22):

supported IMU/ motor driver  list

samuk, 2022-08-22:
## Description

Is there a list of supported IMU anywhere? Or is it just the GY50?

I'd be particularly interested in any of the breakout garden IMU?
https://shop.pimoroni.com/collections/breakout-garden?q=robot

## Definition of Done
Documentation includes list of supported hardware,  or clarifies rhat it is only GY50 that is supported

platisd, 2022-08-22:
Currently only the GY-50 is supported as mentioned in [Supported sensors](https://github.com/platisd/smartcar_shield#supported-sensors)

samuk, 2022-08-22:
Thanks. I might see if I can add support for https://learn.adafruit.com/adafruit-bno055-absolute-orientation-sensor/arduino-code

Closed 2022-08-22.

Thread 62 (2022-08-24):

DRV8830

samuk, 2022-08-24:
## Description

Would you be interested in supporting https://github.com/adafruit/Adafruit_DRV8830 under your library?

## Definition of Done

platisd, 2022-08-24:
Sure, why not? The placeholder I2cMotor class was created with something like that in mind.

samuk, 2022-08-25:
Great! This is the one I'd use https://shop.pimoroni.com/products/drv8830-dc-motor-driver-breakout?variant=30093450739795 there are a few available

platisd, 2022-08-25:
I suggest the following steps forward since I don't have this piece of HW:
1. Get your hands on the hardware
2. Make it work with some library/code
3. Send me a link to that library/code (please do not use software that's licensed under GPL) along with exactly what address were used etc.
4. I integrate it to this library

Does that sound good?

samuk, 2022-08-25:
Great!

Closed 2023-01-23.

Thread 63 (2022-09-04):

BNO055?

samuk, 2022-09-04:
## Description

Add support for https://github.com/adafruit/Adafruit_BNO055

Various open hardware boards are available:
https://www.smart-prototyping.com/Zio-9DOF-IMU-BNO055.html
https://www.adafruit.com/product/4646

If I post you one would you have a go at getting it working?

## Definition of Done

platisd, 2022-09-04:
I'm afraid I can't promise I will have the time for this in the near future so my suggestion is to give it a go yourself first.
Specifically, if you make it adhere to the [HeadingSensor](https://github.com/platisd/smartcar_shield/blob/master/src/sensors/heading/HeadingSensor.hpp)
interface then it's very easy adding it to the rest of the stack.
Looking at this [example](https://github.com/adafruit/Adafruit_BNO055/blob/master/examples/position/position.ino) the `z` is what I believe you should need to expose as "the heading", assuming some reasonable sensor placement on the vehicle.

I will be very happy to assist where I can. Don't know if this will be supported as a standard part of the Smartcar library, but it could definitely be an add-on type of thing.

samuk, 2022-09-06:
OK thanks

Closed 2022-09-06.

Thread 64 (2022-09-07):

Minsumo hardware supported?

samuk, 2022-09-07:
## Description
This Minisumo robot project https://github.com/hansj66/micro-bot/#readme has [similar hardware I](https://docs.google.com/spreadsheets/d/16ljmmDqe1J7KlZV-EWnNo2i8vnV5bdKIFAJKv4D_IHI/edit#gid=2048989373)I  think L293DD is supported under your library?

Assuming the Micro:Bit slot had an ESP32 device inserted would you anticipate any problems getting it to run?

If there are no obvious problems I might do a version with[ hall encoders](https://www.aliexpress.com/item/32857563560.html)

## Definition of Done

samuk, 2022-09-07:
Great, i'll investigate adding some encoder inputs.

Closed 2022-09-07.

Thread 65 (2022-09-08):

Web interface?

samuk, 2022-09-08:
## Description

Would you be interested in adding a web interface like this: https://github.com/701lab/ESP32-robot-car-controller#esp32-robot-car-controller

To your library? It seems like it should be possible: https://github.com/701lab/ESP32-robot-car-controller/issues/2#issuecomment-1237977819

## Definition of Done

platisd, 2022-09-09:
It surely is possible but I don't see how this is some functionality that should be included in this library. :)
`smartcar_shield` is all about abstracting the control of different common mechanical and digital components on a miniature car, not include the entire stack necessary for communication, UI etc.
Additionally, including something like this would "tie" the library to ESP32 or at least WiFi-capable microcontrollers, which is not a direction we should go.

samuk, 2022-09-09:
I thought you might say that :) I'll look into doing this as a separate repo.

Thinking about it a bit more it would be interesting to be able to access more of the API than simple steering control. Something more like https://github.com/ayushsharma82/WebSerial

platisd, 2022-09-09:
Take a look at this example of [Smartcar controls and sensors being exposed via a REST API](https://github.com/DIT112-V20/kotlin-app-arduino-sketch-ci/blob/master/arduino/SmartcarWebserver/SmartcarWebserver.ino).

Closed 2022-09-09.

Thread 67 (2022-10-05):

Motor driver abstraction

samuk, 2022-10-05:
## Description

This lib seems to do a nice job of abstracting motor drivers: https://github.com/tfeldmann/Arduino-MotorDriver

Could you provide some example code for how you would integrate that with your library?

## Definition of Done

It's clear how to use various types of motor driver with the Smartcar_shield library.

platisd, 2022-10-05:
This library already does the same thing too (among others). Why would you like to integrate it?

Closed 2023-01-14.

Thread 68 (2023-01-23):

Arduino lib for additional IMU

samuk, 2023-01-23:
## Description
Support additional common IMU

## Definition of Done
Add support the IMU supported by this Arduino Lib: https://github.com/torehan/arduino-mpu-driver/blob/master/src/MPU.cpp#L153

platisd, 2023-01-24:
What exactly do you want to do here?
Not sure I follow. 🤔

samuk, 2023-01-24:
I want to make a robot that works with a variety of common IMU.

platisd, 2023-01-24:
Usually a robot has a specific chip for its IMU, why would you want it to work with a variety of them in the first place?

Also, since this library already exists, why would we duplicate this work? At the best case one would need to interface this library your referring to with the Smartcar one, not integrate it.

samuk, 2023-01-24:
I'm interested in making open hardware components that are useful to other hobbyists. One of those components may be a chassis loosely based on your platform

Similar in concept ro this https://shop.pimoroni.com/products/trilobot?variant=39594077093971 the manufacturer doesn't specify which I2C sensors you must use.

,The more components supported 'out of the box' the better the initial experience for the builder.

platisd, 2023-01-24:
In the example you sent, they don't specify which sensors to use because they don't support any sensors with their library. 🤷‍♂️

The idea of supporting "as many things as possible" is attractive in the development of any library or product, however it contains risks (e.g. it will be harder for users to discover the functionality they want if there's too much of it) and also requires a lot of maintenance.
Personally, if I don't know how a sensor works, not even own I or see the need for making it a part of the hardware reference platform, it doesn't make sense to start supporting it software-wise.

This library instead allows for new sensors to be **interfaced** with it. I think I've mentioned this before, but if a class provided by the user implements the `HeadingSensor` interface, then it can be used _along with_ the Smartcar library.

So my suggestion is to go one of the following roads:
1. Pick a sensor and provide support for it. If it's the `GY-50` then support for it is baked into this library.
2. Don't provide any support and leave this responsibility for your users, allowing them to interface the software library with custom sensors.
3. Create a new library, eg `Smartcar_IMU.h` that wraps up those IMU sensors into new classes that implement the correct interface. Then the users can get that new library and use it along the Smartcar one.

I can provide some guidance for the last "road" but I'm not going to implement it myself since my time is limited.

samuk, 2023-01-24:
Thanks, my thought is to adapt your 'motors' board slightly and make it wider so [Nano ITX compute](https://github.com/Twisted-Fields/acorn-robot-electronics/issues/2#issuecomment-1399501675) modules fit on it. Retain the position & electrical/signal compatibility with your existing [inter-board connector headers](https://github.com/adityakamath/akros2_bringup/issues/).

The idea is users could start their robotics with your existing ESP32 modules board, but later add an additional RPI or [CM4 based compute module](https://github.com/Twisted-Fields/acorn-robot-electronics/issues/2#issuecomment-1399501675) on top to run [PythonRobotics](https://atsushisakai.github.io/PythonRobotics/getting_started.html) or [Linorobot2 ](https://github.com/linorobot/linorobot2/#linorobot2)

I'd add pinout for three connector types [Breakout garden](https://shop.pimoroni.com/collections/breakout-garden), [UEXT ](https://www.olimex.com/Products/Modules/) & [mikroBUS](https://www.mikroe.com/mikrobus-shuttle-127mm-2x8-pin-box-header-smd-male) probably leaving the actual connectors unpopulated in any board runs.

I realise there's no such thing as a universal robot platform, and there are risks in trying to be all things to all people. I am however drawn to seeing what's possible with modularity and testing the edges of interoperability.

 I suppose this is a long-winded way of going for your 2) to focus on hardware, then hope that people find the hardware useful and improve the software.

I may of course just abandon the idea as overambitious, or I may get around to doing some PCB's.

platisd, 2023-01-24:
Sounds good. Oh also, I don't know your background (mine is in software) but -electrically- the current PCB design is not optimal, i.e. the AA batteries are often not enough to power everything up.
Just something to keep in mind before repeating the mistakes I did. :sweat_smile:

samuk, 2023-01-24:
Yeah I've been browsing [Lipo](https://www.aliexpress.com/w/wholesale-3s-lipo-2000mah-charger.html) Your power traces are super thin too!

I think to make room for the Lipo the [TB6612FNG](https://www.sparkfun.com/products/14451) would need to go on the underside of the board next to the motors.

platisd, 2023-01-24:
Looking forward to see what you create :+1:

samuk, 2023-01-31:
Done a bit of thinking/hacking on this concept: https://github.com/rosmo-robot/smartcar_shield#proposed-smartcar-20-development

Thinking to go for two motor drivers to enable mecanum drive. Do you have any feedback on the concept before we start the proper PCB design?

platisd, 2023-01-31:
Looks nice, where will the batteries go?

samuk, 2023-01-31:
Between the Motors board and the Modules board. (The motor drivers will be moved to the underside of the motors board to facilitate this)

~11.1v goes direct to the motors board. The modules board receives 5V USB direct from https://www.aliexpress.com/item/1005003593209704.html (or Via the RPI/Jetson/whatever if one is used)

platisd, 2023-01-31:
Nice, just make sure everything fits I guess. Can't comment much on the "electric" part of things as I'm not the most knowledgeable. 😅

samuk, 2023-02-09:
I think we've mostly finished the new 'motors' board

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

Ended up with quite a few changes compared your original;

* Dual SMT motor drivers
* On-board bucks
* LiFePO4 batteries
* 2 x 40pin board interconnect headers

We're tarting work on the 'modules' board soon: https://raw.githubusercontent.com/rosmo-robot/smartcar_shield/master/extras/images/modules.png

Optional SBC would mount above this.

I don't know if you have a preference for continuing to call this hardware 'Smartcar 2.0' or would you prefer it if we call it something different?  Started a bit of documentation here: https://rosmo-robot.github.io/aboutme/

I'd quite like to call it 'Rosmo' but interested in your thoughts.

platisd, 2023-02-09:
You're doing some great work, keep it up! :+1:

And you can call it however you like, I at least consider it as novel work. :)

samuk, 2023-03-11:
Progress on the derivative Rosmo board is happening slowly.

I've opened three issues which we need to resolve before the derivative Rosmo/ Smartcar2 robot will run your lib https://github.com/rosmo-robot/smartcar_shield/issues any input on those would be welcome, particularly how to best handle dual motor drivers:  https://github.com/rosmo-robot/smartcar_shield/issues/1

Closed 2023-01-24.

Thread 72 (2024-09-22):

The code doesn't compile for the latest Arduino IDE and ESP32 Nano board

platisd, 2024-09-22:
`analogWrite.h` is not found anymore, probably it's now properly included in the Arduino layer.

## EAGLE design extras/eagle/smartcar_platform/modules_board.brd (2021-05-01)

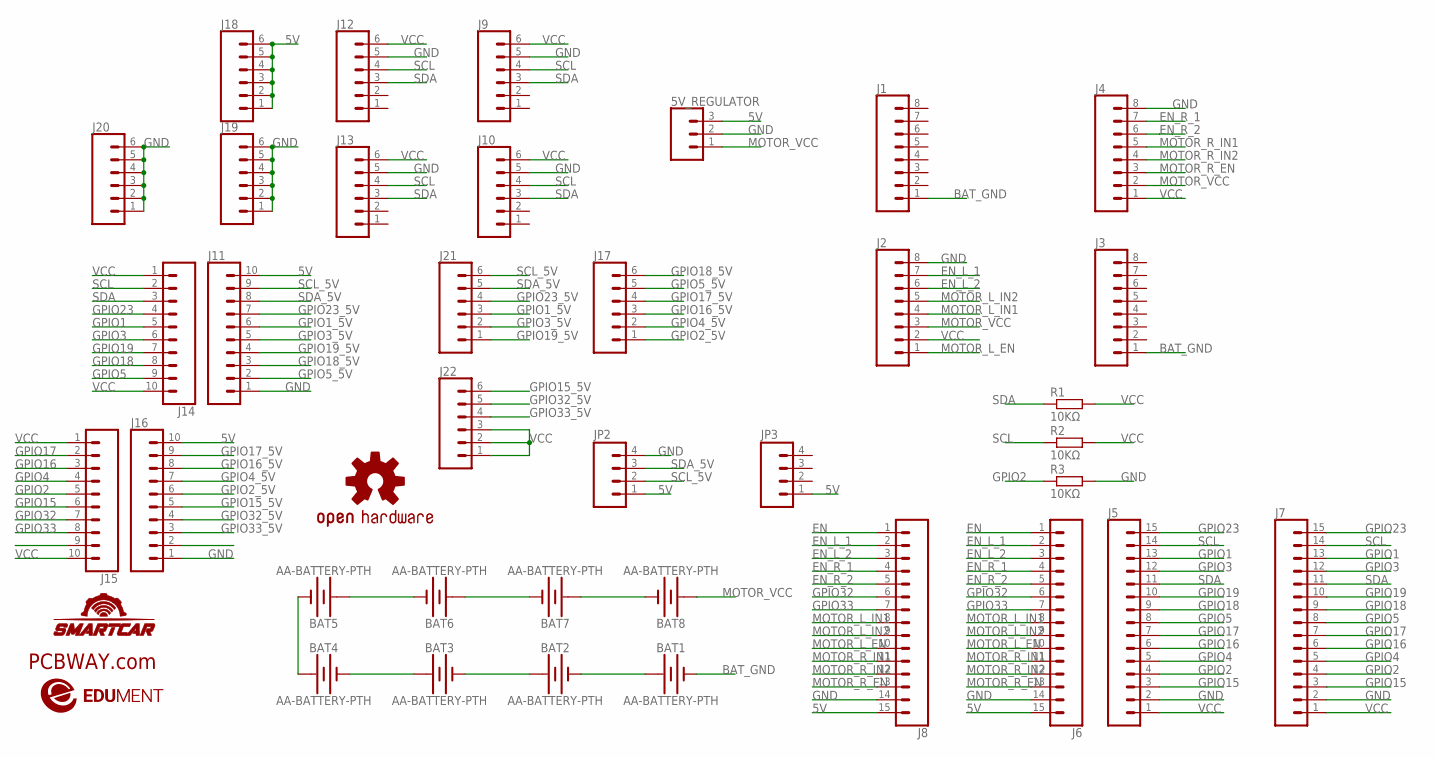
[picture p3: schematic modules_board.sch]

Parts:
5V_REGULATOR: CONN_03LOCK; 1X03_LOCK
BAT1, BAT2, BAT3, BAT4, BAT5, BAT6, BAT7, BAT8: AA-BATTERY-PTH; AA-PCB-BATTERY
J1, J2, J3, J4: CONN_08NO_SILK_FEMALE_PTH; 1X08_NO_SILK
J5, J6: CONN_15LOCK_LONGPADS; 1X15_LOCK_LONGPADS
J7, J8: CONN_15LOCK_NO_SILK; 1X15_LOCK_NO_SILK
J9, J10, J12, J13, J17, J18, J19, J20, J21, J22: CONN_06LOCK; 1X06_LOCK
J11, J14, J15, J16: CONN_10"; 1X10
JP2, JP3: M04NO_SILK_ALL_ROUND; 1X04_NO_SILK_ALL_ROUND
LOGO1: OSHW-LOGOL; OSHW-LOGO-L
R1, R2, R3: 10KΩ; 0207/12
SMRTCR1: SMARTCAR_LOGOMEDIUM; SMARTCAR_LOGO_MEDIUM
U$1: PCBWAY_LOGO
U$2: EDUMENT_LOGOLARGE; EDUMENT_LOGO_LARGE

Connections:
5V: 5V_REGULATOR.3, J6.15, J8.15, J11.10, J16.10, J18.1, J18.2, J18.3, J18.4, J18.5, J18.6, JP2.1, JP3.1
BAT_GND: BAT1.NEG (-), J1.1, J3.1
EN: J6.1, J8.1
EN_L_1: J2.7, J6.2, J8.2
EN_L_2: J2.6, J6.3, J8.3
EN_R_1: J4.7, J6.4, J8.4
EN_R_2: J4.6, J6.5, J8.5
GND: 5V_REGULATOR.2, J2.8, J4.8, J5.2, J6.14, J7.2, J8.14, J9.5, J10.5, J11.1, J12.5, J13.5, J16.1, J19.1, J19.2, J19.3, J19.4, J19.5, J19.6, J20.1, J20.2, J20.3, J20.4, J20.5, J20.6, JP2.4, R3.2
GPIO1: J5.13, J7.13, J14.5
GPIO1_5V: J11.6, J21.3
GPIO2: J5.4, J7.4, J15.5, R3.1
GPIO2_5V: J16.6, J17.1
GPIO3: J5.12, J7.12, J14.6
GPIO3_5V: J11.5, J21.2
GPIO4: J5.5, J7.5, J15.4
GPIO4_5V: J16.7, J17.2
GPIO5: J5.8, J7.8, J14.9
GPIO5_5V: J11.2, J17.5
GPIO15: J5.3, J7.3, J15.6
GPIO15_5V: J16.5, J22.6
GPIO16: J5.6, J7.6, J15.3
GPIO16_5V: J16.8, J17.3
GPIO17: J5.7, J7.7, J15.2
GPIO17_5V: J16.9, J17.4
GPIO18: J5.9, J7.9, J14.8
GPIO18_5V: J11.3, J17.6
GPIO19: J5.10, J7.10, J14.7
GPIO19_5V: J11.4, J21.1
GPIO23: J5.15, J7.15, J14.4
GPIO23_5V: J11.7, J21.4
GPIO32: J6.6, J8.6, J15.7
GPIO32_5V: J16.4, J22.5
GPIO33: J6.7, J8.7, J15.8
GPIO33_5V: J16.3, J22.4
MOTOR_L_EN: J2.1, J6.10, J8.10
MOTOR_L_IN1: J2.4, J6.8, J8.8
MOTOR_L_IN2: J2.5, J6.9, J8.9
MOTOR_R_EN: J4.3, J6.13, J8.13
MOTOR_R_IN1: J4.5, J6.11, J8.11
MOTOR_R_IN2: J4.4, J6.12, J8.12
MOTOR_VCC: 5V_REGULATOR.1, BAT8.POS (+), J2.3, J4.2
unnamed: BAT2.POS (+), BAT3.NEG (-)
unnamed: BAT1.POS (+), BAT2.NEG (-)
unnamed: BAT3.POS (+), BAT4.NEG (-)
unnamed: BAT4.POS (+), BAT5.NEG (-)
unnamed: BAT5.POS (+), BAT6.NEG (-)
unnamed: BAT6.POS (+), BAT7.NEG (-)
unnamed: BAT7.POS (+), BAT8.NEG (-)
SCL: J5.14, J7.14, J9.4, J10.4, J12.4, J13.4, J14.2, R2.1
SCL_5V: J11.9, J21.6, JP2.2
SDA: J5.11, J7.11, J9.3, J10.3, J12.3, J13.3, J14.3, R1.1
SDA_5V: J11.8, J21.5, JP2.3
VCC: J2.2, J4.1, J5.1, J7.1, J9.6, J10.6, J12.6, J13.6, J14.1, J14.10, J15.1, J15.10, J22.1, J22.2, J22.3, R1.2, R2.2

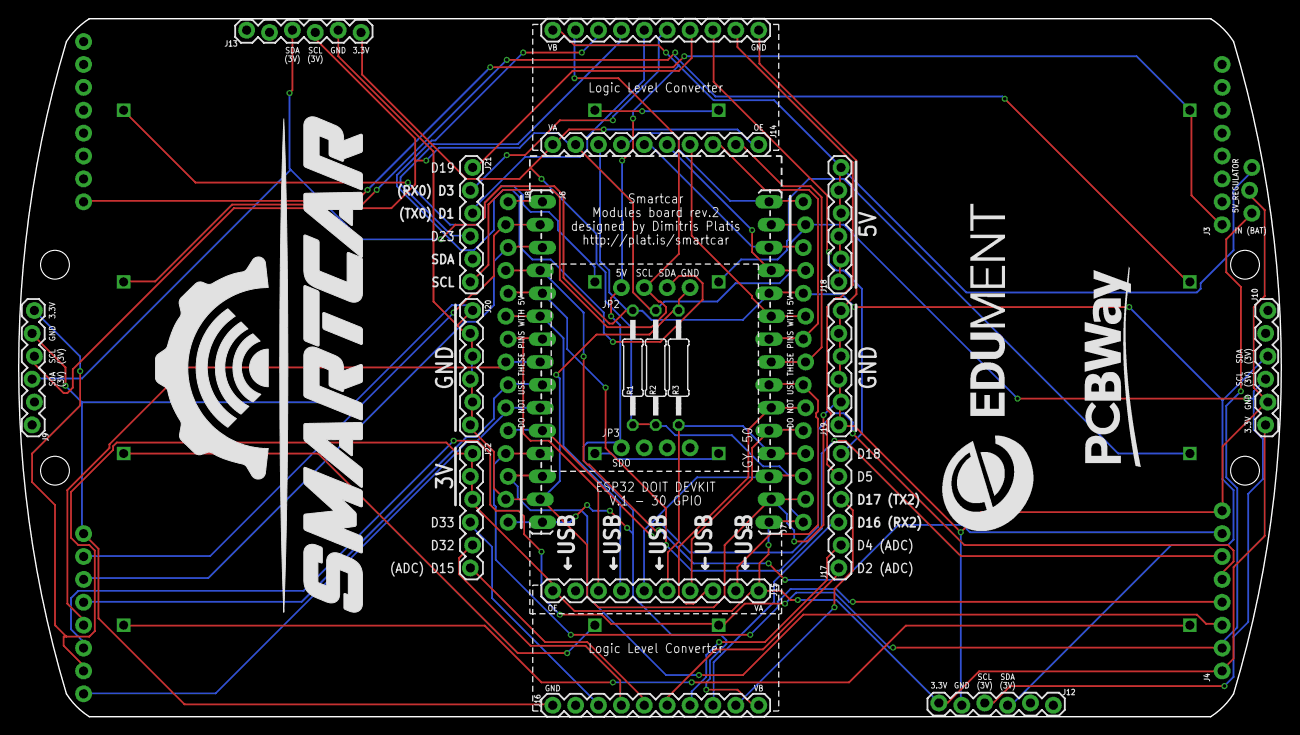
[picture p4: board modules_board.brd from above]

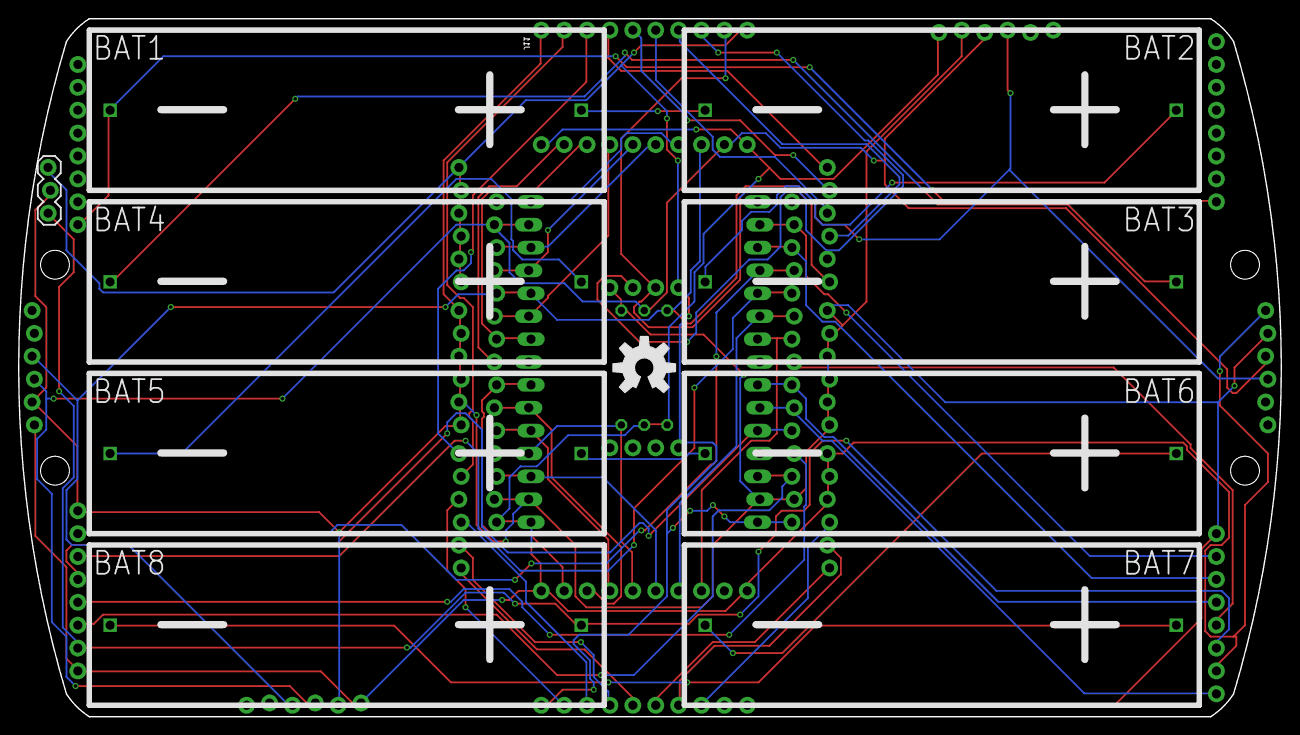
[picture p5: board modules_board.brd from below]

Board: 2 copper layers, 140.1 x 77.5 mm, 40 parts (10 on the bottom side), 53 nets.

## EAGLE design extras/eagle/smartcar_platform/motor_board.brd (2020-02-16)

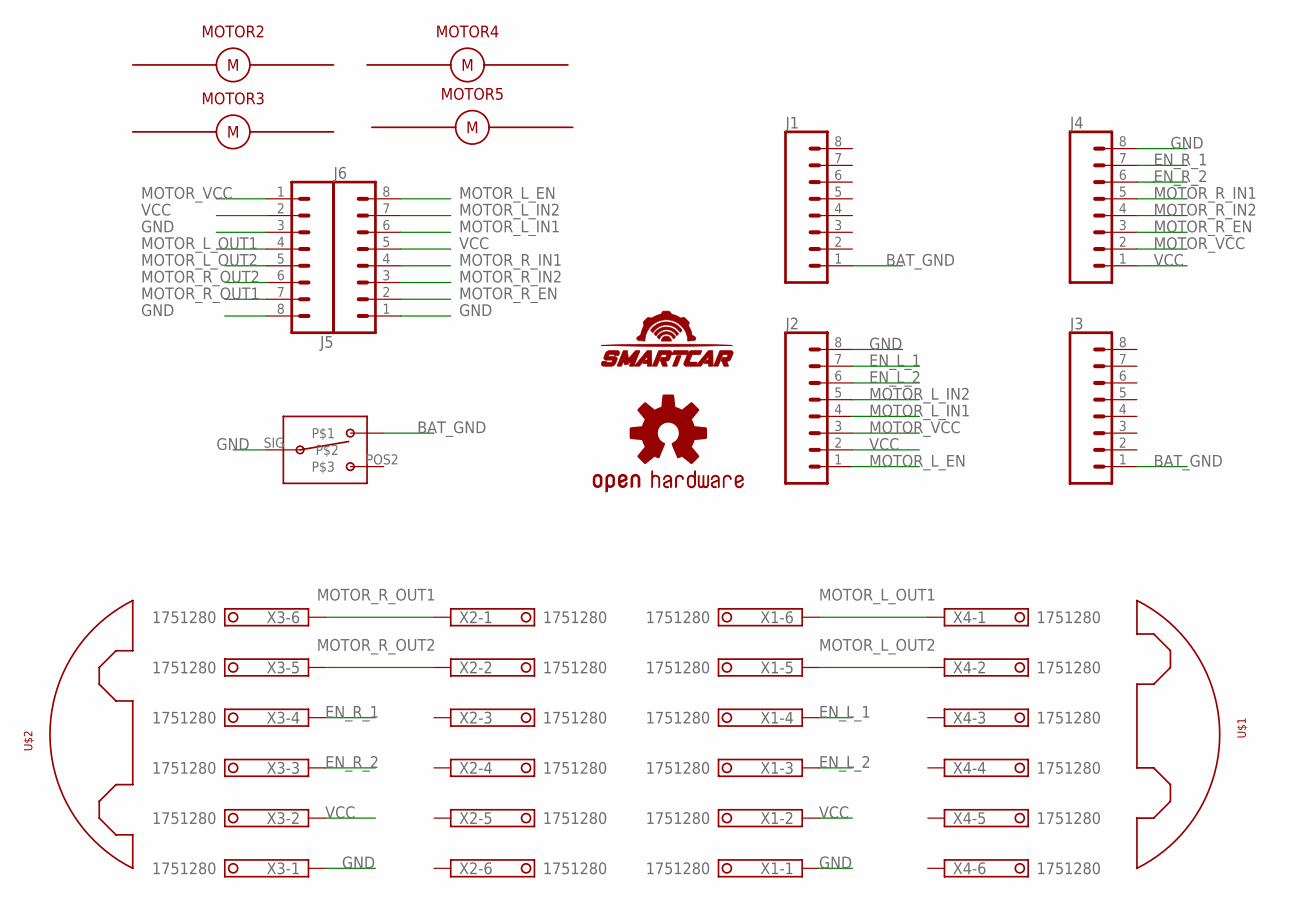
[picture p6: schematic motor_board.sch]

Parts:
J1, J2, J3, J4: CONN_08NO_SILK_FEMALE_PTH; 1X08_NO_SILK
J5, J6: CONN_08"; 1X08
LOGO1: OSHW-LOGOL; OSHW-LOGO-L
MOTOR2, MOTOR3, MOTOR4, MOTOR5: SMARTCAR_MOTOR; SMARTCAR_MOTOR_MOUNT_HOLES
SMRTCR1: SMARTCAR_LOGOMEDIUM; SMARTCAR_LOGO_MEDIUM
SW1: SPDT-HIGH-AMP-SWITCHPTH; SPDT-0.2-THICK-PINS
U$1, U$2: BUMPER_020522_SCREWS; BUMPER_2_SCREWS_NARROW
X1, X2, X3, X4: 1751280

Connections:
BAT_GND: J1.1, J3.1, SW1.POS1
EN_L_1: J2.7, X1.4
EN_L_2: J2.6, X1.3
EN_R_1: J4.7, X3.4
EN_R_2: J4.6, X3.3
GND: J2.8, J4.8, J5.3, J5.8, J6.1, SW1.SIG, X1.1, X3.1
MOTOR_L_EN: J2.1, J6.8
MOTOR_L_IN1: J2.4, J6.6
MOTOR_L_IN2: J2.5, J6.7
MOTOR_L_OUT1: J5.4, X1.6, X4.1
MOTOR_L_OUT2: J5.5, X1.5, X4.2
MOTOR_R_EN: J4.3, J6.2
MOTOR_R_IN1: J4.5, J6.4
MOTOR_R_IN2: J4.4, J6.3
MOTOR_R_OUT1: J5.7, X2.1, X3.6
MOTOR_R_OUT2: J5.6, X2.2, X3.5
MOTOR_VCC: J2.3, J4.2, J5.1
VCC: J2.2, J4.1, J5.2, J6.5, X1.2, X3.2

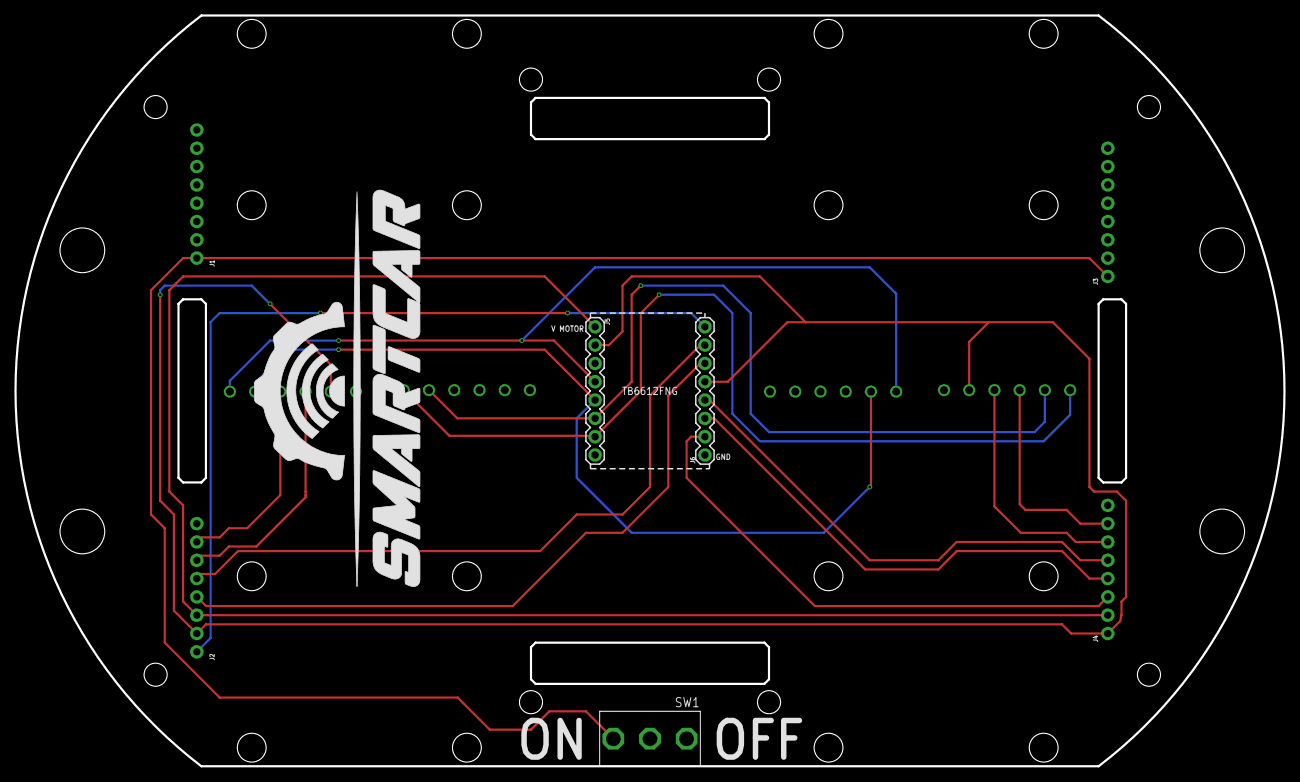
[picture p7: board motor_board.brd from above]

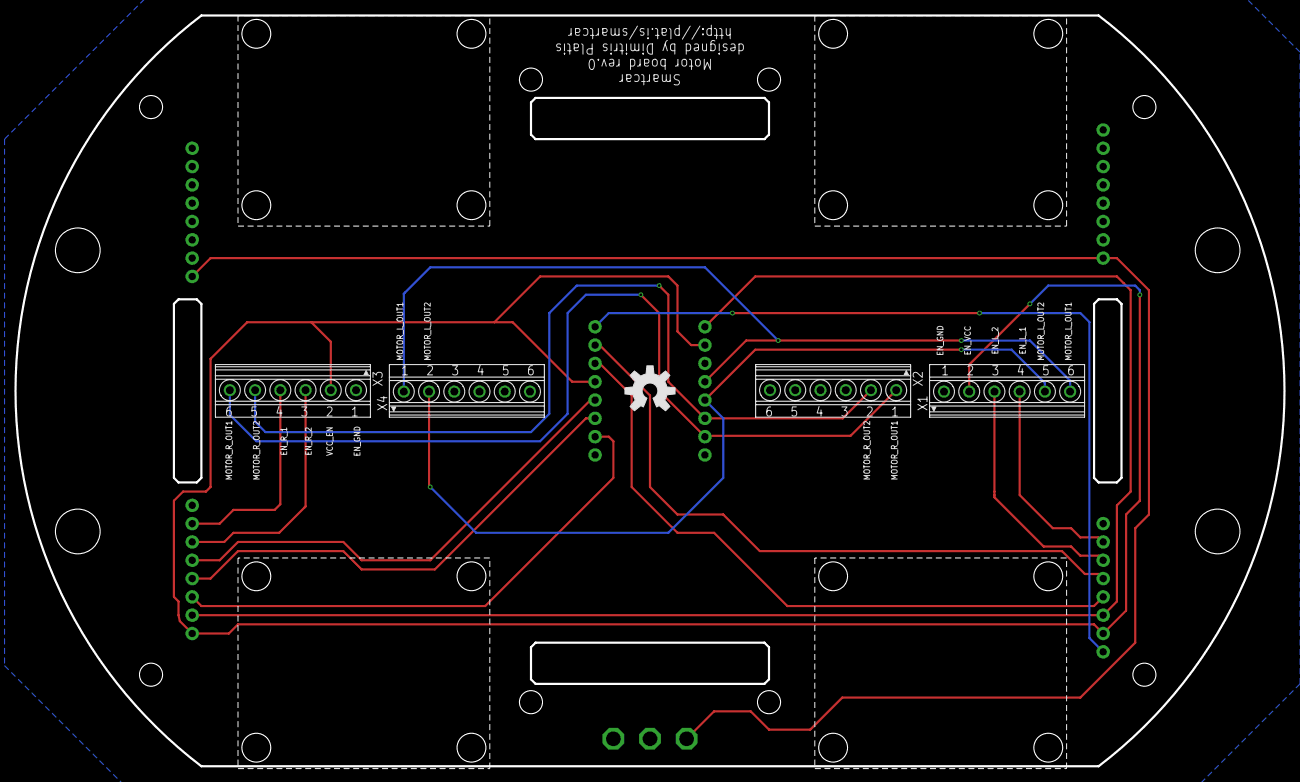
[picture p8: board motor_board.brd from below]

Board: 2 copper layers, 176.0 x 104.1 mm, 19 parts (9 on the bottom side), 18 nets.

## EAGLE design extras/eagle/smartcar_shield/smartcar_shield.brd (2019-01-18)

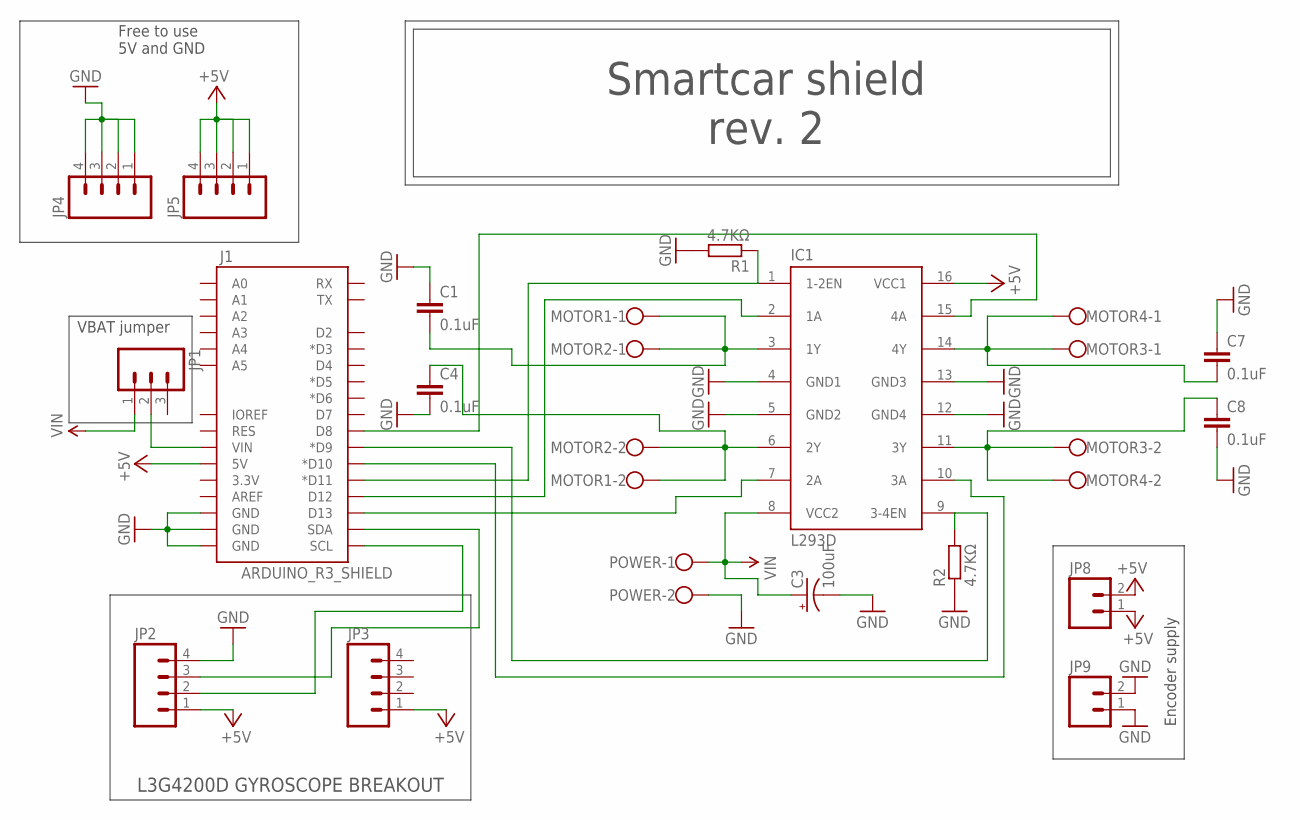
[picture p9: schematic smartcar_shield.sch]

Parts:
C1, C4, C7, C8: 0.1uF; CAP-PTH-SMALL-KIT
C3: 100uF; CPOL-RADIAL-10UF-25V
IC1: L293D; DIL16
J1: ARDUINO_R3_SHIELD; UNO_R3_SHIELD
JP1: M03PTH; 1X03
JP2, JP3, JP4, JP5: M04NO_SILK_ALL_ROUND; 1X04_NO_SILK_ALL_ROUND
JP8, JP9: M021X02_NO_SILK; 1X02_NO_SILK
MOTOR1, MOTOR2, MOTOR3, MOTOR4: W237-102
POWER: W237-102
R1, R2: 4.7KΩ; 0207/10

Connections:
12V: C3.1 (+), IC1.8 (VCC2), JP1.1, POWER.1
+5V: IC1.16 (VCC1), J1.5V, JP2.1, JP3.1, JP5.1, JP5.2, JP5.3, JP5.4, JP8.1, JP8.2
ENABLE1: IC1.1 (1-2EN), J1.D11 (*D11), R1.1
ENABLE2: IC1.9 (3-4EN), J1.D9 (*D9), R2.2
GND: C1.1, C3.2 (-), C4.2, C7.1, C8.2, IC1.4 (GND1), IC1.5 (GND2), IC1.12 (GND4), IC1.13 (GND3), J1.GND@0 (GND), J1.GND@1 (GND), J1.GND@2 (GND), JP2.4, JP4.1, JP4.2, JP4.3, JP4.4, JP9.1, JP9.2, POWER.2, R1.2, R2.1
MOTORA-1: IC1.2 (1A), J1.D12
MOTORA-2: IC1.7 (2A), J1.D13
MOTORA-OUT1: C1.2, IC1.3 (1Y), MOTOR1.1, MOTOR2.1
MOTORA-OUT2: C4.1, IC1.6 (2Y), MOTOR1.2, MOTOR2.2
MOTORB-1: IC1.15 (4A), J1.D8
MOTORB-2: IC1.10 (3A), J1.D10 (*D10)
MOTORB-OUT1: C7.2, IC1.14 (4Y), MOTOR3.1, MOTOR4.1
MOTORB-OUT2: C8.1, IC1.11 (3Y), MOTOR3.2, MOTOR4.2
unnamed: J1.SDA, JP2.3
SCL: J1.SCL, JP2.2
VIN: J1.VIN, JP1.2

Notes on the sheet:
Encoder supply
Free to use 5V and GND
VBAT jumper
Smartcar shield rev. 2
L3G4200D GYROSCOPE BREAKOUT

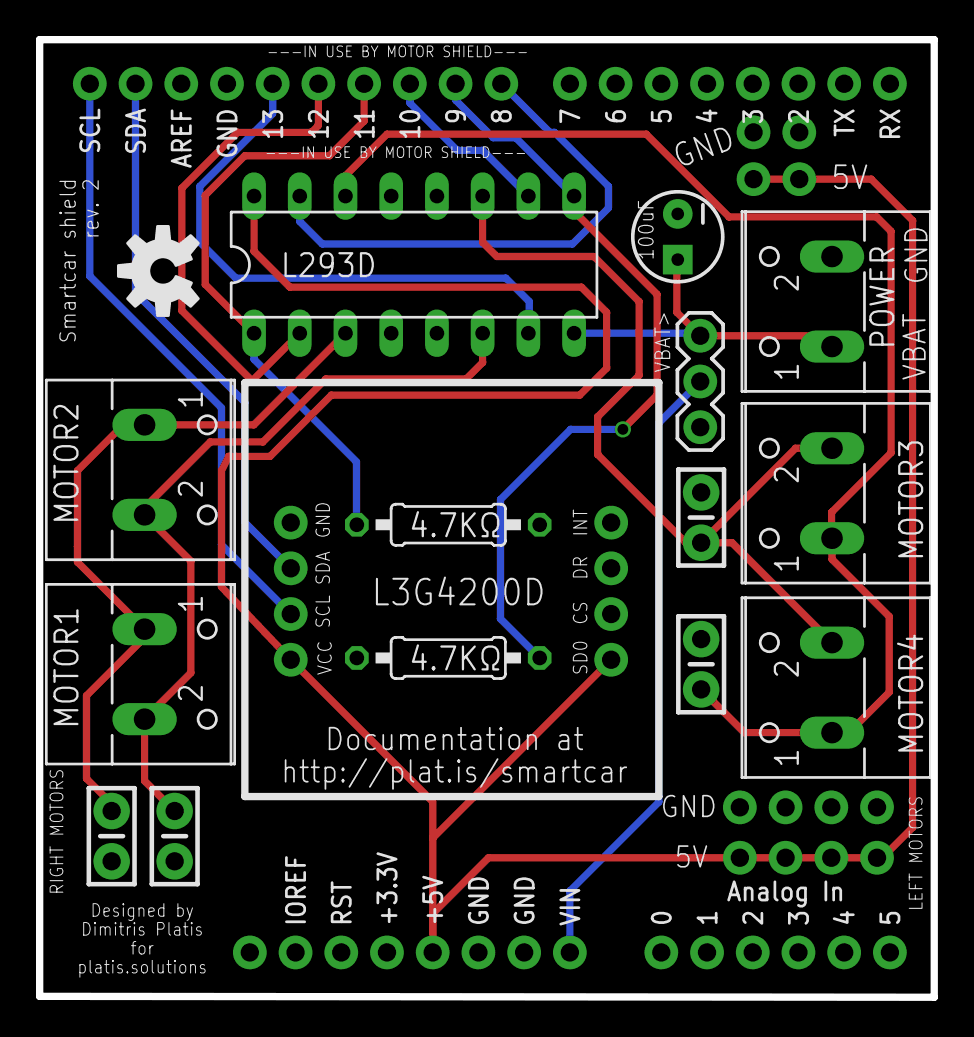
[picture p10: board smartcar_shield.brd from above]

Board: 2 copper layers, 49.7 x 53.2 mm, 22 parts (0 on the bottom side), 16 nets.

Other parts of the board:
U$1: OSHW-LOGO-M

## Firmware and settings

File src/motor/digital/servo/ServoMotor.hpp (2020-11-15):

/**
 * \class ServoMotor
 * A motor that is controlled via the length of pulses that are sent to it
 * through a single signal line.
 * It can be either a traditional servo motor that controls a shaft (e.g. for steering)
 * or an Electronic Speed Controller (ESC) that interpets speed in the same manner
 * and controls a (typically brushless) motor.
 */
#pragma once

#include <Servo.h>
#include <stdint.h> // NOLINT(modernize-deprecated-headers)

#include "../../Motor.hpp"

namespace smartcarlib
{
namespace constants
{
namespace servomotor
{
const int kDefaultMinPulseLength  = 1000;
const int kDefaultIdlePulseLength = 1500;
const int kDefaultMaxPulseLength  = 2000;
} // namespace servomotor
} // namespace constants
} // namespace smartcarlib

class ServoMotor : public Servo, public Motor
{
public:
    /**
     * Constructs a servo motor
     * @param controlPin      The pin controlling the speed of the motor
     * @param minPulseLength  The motor's minimum pulse length in microseconds
     * @param idlePulseLength The pulse length that the motor is idle in microseconds
     * @param maxPulseLength  The motor's maximum pulse length in microseconds
     *
     * **Example:**
     * \code
     * const unsigned short ESC_PIN = 7;
     * ServoMotor esc(ESC_PIN);
     * \endcode
     */
    ServoMotor(uint8_t controlPin,
               int minPulseLength  = smartcarlib::constants::servomotor::kDefaultMinPulseLength,
               int idlePulseLength = smartcarlib::constants::servomotor::kDefaultIdlePulseLength,
               int maxPulseLength  = smartcarlib::constants::servomotor::kDefaultMaxPulseLength);

    /* Check `Motor` interface for documentation */
    void setSpeed(int speed) override;

private:
    const uint8_t kControlPin;
    const int kMinPulseLength;
    const int kIdlePulseLength;
    const int kMaxPulseLength;
    bool mAttached;
};

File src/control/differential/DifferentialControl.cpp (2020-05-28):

#include "DifferentialControl.hpp"

#include "../../utilities/Utilities.hpp"

using namespace smartcarlib::utils;
using namespace smartcarlib::constants::control;
using namespace smartcarlib::constants::motor;

DifferentialControl::DifferentialControl(Motor& leftMotor, Motor& rightMotor)
    : mLeftMotor(leftMotor)
    , mRightMotor(rightMotor)
    , mAngle{ 0 }
    , mSpeed{ 0 }
{
}

void DifferentialControl::setAngle(int angle)
{
    mAngle = getConstrain(angle, kMinControlAngle, kMaxControlAngle);
    setMotors();
}

void DifferentialControl::setSpeed(int speed)
{
    mSpeed = getConstrain(speed, kMinMotorSpeed, kMaxMotorSpeed);
    setMotors();
}

void DifferentialControl::setMotors()
{
    // With differential control, angle represents the ratio of speed between the two motors
    float ratio = static_cast<float>(kMaxControlAngle - getAbsolute(mAngle))
                  / static_cast<float>(kMaxControlAngle);

    if (mAngle < kIdleControlAngle)
    {
        // Turning to the left (counter clockwise) by setting lower speed to the left motor
        mLeftMotor.setSpeed(static_cast<int>(static_cast<float>(mSpeed) * ratio));
        mRightMotor.setSpeed(mSpeed);
    }
    else
    {
        // Turning to the right (clockwise) by setting lower speed to the right motor
        mLeftMotor.setSpeed(mSpeed);
        mRightMotor.setSpeed(static_cast<int>(static_cast<float>(mSpeed) * ratio));
    }
}

void DifferentialControl::overrideMotorSpeed(int firstMotorSpeed, int secondMotorSpeed)
{
    firstMotorSpeed  = getConstrain(firstMotorSpeed, kMinMotorSpeed, kMaxMotorSpeed);
    secondMotorSpeed = getConstrain(secondMotorSpeed, kMinMotorSpeed, kMaxMotorSpeed);

    mLeftMotor.setSpeed(firstMotorSpeed);
    mRightMotor.setSpeed(secondMotorSpeed);
}

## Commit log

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2015-02-17 Smartcar sensors header file, updated to version 0.3 that includes the gyroscope, the NewPing timer and compatibility with the Smartcar Core library
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2015-02-17 added compatibility with gp2d120 in commented out code. It's not incorporated into the library because usually the sensors used are of just one kind
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2015-05-09 changed declaration type of throttleFreq to unsigned short
2015-05-12 updated getAngle and getSpeed so to provide the speed the user entered not the frequency sent to the servo and the ESC
2015-05-15 changing pin declarations to unsigned short
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2015-05-20 changed the sampling rate of the gyroscope, so to produce more accurate results
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2015-10-08 LED driver's utilities
    [led_driver.brd, led_driver.sch]
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2015-11-05 removed useless interrupts() call and fixed sign in the returned angles
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2015-11-06 we don't disable interrupts anymore as this causes disturbances to interrupt based operations
2015-11-13 removing non-applicable resources
    [led_driver.brd, led_driver.sch]
2015-11-13 adding eagle car sketches
    [smartcar_shield.GBL, smartcar_shield.GBO, smartcar_shield.GBP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]
2015-11-13 revert to older commit
    [smartcar_shield.GBL, smartcar_shield.GBO, smartcar_shield.GBP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]
2015-11-13 eagle CAD files for the smartcar shield PCB
    [smartcar_shield.brd, smartcar_shield.sch]
2015-11-18 various small fixes and calibration method
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2015-11-29 smartcar shield rev. 1
    [smartcar_shield.brd, smartcar_shield.sch]
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2015-11-30 go to cruise mode only if at least one encoder was attached
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2015-12-05 added check if i2c is already started and if no number of measurements was supplied to calibrate
2015-12-05 refactoring library to new standard
    [smartcar_shield.brd, smartcar_shield.sch]
2015-12-06 changing from uint8_t to unsigned short so to abide by arduino's guidelines
    [SRF08.cpp]
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2016-01-21 adding 2D and 3D cad files
    [SmartCar_chassis.dwg, SmartCar_chassis.dxf]
2016-01-24 v 3.0.1 includes fixed Gyroscope::calibrate function
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2016-01-26 removing NewPing class, due to possible interferences with the PWM output of Timer2 on pin 9
2016-01-29 Heading sensor represents various sensors that can provide heading (gyroscope, imu, magnetometer)
2016-01-29 adding heading sensor class, refactoring begin, now the heading sensor and odometers are used by reference, without creating their copies
2016-01-29 small fix in rotate, begin refactored to use heading sensors and odometers by reference, using heading sensor instead of gyroscope
2016-01-29 example that controls a car which uses an ESC to throttle and a servo to steer
2016-02-01 Adjusting the values in the ESC motor so it makes more sense for the average use cases
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2016-02-02 microseconds are used now to increase accuracy and filter out jitter
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2016-02-11 chassis in dxf format without axes or dimensions for easier milling in cnc's
    [SmartCar_chassis_NoAxesDimensions.dxf]
2016-02-11 removing libraries that are already included by Arduino.h and compatibility with very old IDEs
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2016-05-09 the simple brushed dc motors are represented now programmatically. they can be used both for throttling and steering (on very cheap rc cars)
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2016-07-14 updating the steering with dc motors in order to better represent the way those motors work
2016-07-23 Revert to the old way of steering the car with a dc motor
    This reverts commit 43f2d9a2add2855990b532cbed91099c6f3be214.
2016-07-23 Revert "Revert to the old way of steering the car"
    This reverts commit f7f7fe6bd234c4cd05e5e7019afe7cde14f6ef9c.
2016-07-23 typo fix, thanks to NickCh1996@017fc0ce2131b700c40f92587bca345a1c373503
    [FullSerialControl.ino]
2016-07-23 change to facilitate the use of LEFT, RIGHT and FORWARD in setAngle particularly helpful when steering with a single DC motor
2017-01-13 Revert "Converting all tabs to spaces for better readability"
    This reverts commit 8ecdb850d133f14322a924ca276842a12f054462 so to make merging
    with hackathon branch easier.
    [SRF08.cpp, ServoMotor.cpp]
2017-01-16 new getDirection and Car class constructor For odometers that can provide the direction of movement and a Car with two motors attached to arbitrary pins
2017-01-16 user to set the state the direction pin should be in when going forward
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2018-04-07 Bump library version with i2c blocking fix
2018-07-15 Use a single tab field separator in keywords.txt
    Each field of keywords.txt is separated by a single true tab. When you use multiple tabs it causes the field to be interpreted as empty. On Arduino IDE 1.6.5 and newer an empty KEYWORD_TOKENTYPE caus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
    Reference:
    https://github.com/arduino/Arduino/wiki/Arduino-IDE-1.5:-Library-specification#keywords
2018-07-24 Abide by Arduino library structure
    Since source files cannot be placed inside subfolders
    there's little point keeping them directly inside include/
2018-07-26 Rename Steering to Control
    Since we will be having the Steering-Throttling concepts
    later on, it's best to decouple these to avoid confusion
    [Control.hpp]
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2018-10-14 Add new Odometer implementation
    TODO: Fix missing unit tests
    [ArduinoRuntime.cpp, Runtime.hpp]
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2018-10-30 Rename motor to motors
    Naming should be consistent with that of sensors
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2018-11-03 Update travis configuration to use correct compiler
    The current avr-gcc version is 5.4.0 so we should use a similar one
    for the test environment
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2018-11-04 Make SHARP sensor pin a constructor argument
    This will eliminate misuse and simplify the code
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2018-11-04 Eliminate the need for the user to attach() the sensor
    All needed initialization will be done (if not already done)
    when probing the sensor.
2018-11-04 Move all source code out of include folder
    Since we are following the Arduino file structure
    having an include/ folder does not make much sense,
    especially since it contained source code as well.
2018-11-05 Enable individual motor control
    In some cases advanced users find it useful to be able
    to control each motor on the car individually.
2018-11-05 getDistance to always return relative distance
    This will make controlling them via higher level of
    abstraction easier and will make the API more consistent.
    Additionally, an isAttached() method was added to the
    Odometer interface so to be able to determine whether the
    sensor was correctly attached, since we cannot ensure that
    during compile time like in other cases.
2018-11-05 Do not set pin direction if attach failed
2019-01-16 Fix measurement timeout
    * Time that sound needs to make a roundtrip is not equal to time
    that is needed for the sensor to make a measurement. Therefore an
    update is necessary in order to be able to conduct measurements up
    to our specified maximum distance.
    * Measurements larger than the max distance return error.
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2019-01-17 Update board to rev. 2
    [smartcar_shield.brd, smartcar_shield.sch]
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2019-01-19 Treat all compiler warnings as errors
    * Fix warnings so the tests can compile
    [GY50.cpp]
2019-01-20 Add examples to function level documentation
    * Also moved attach() method to Odometer interface
2019-01-20 Expect attach calls
    Currently, these two expectations are there only for the coverage.
    Unfortunately, due to how Arduino handles external interrupt
    registrations (and particularly the lack of an std::function
    implementation or the ability to attach interrupts before setup)
    we need the user to call attach manually, outside the library.
    Ideally, attach should not even be needed to be called
    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
2019-01-22 Refactor to build library on esp8266
    Seems like esp8266 uses a rather different g++ so some syntax was
    not compatible with it. Interesting to know that compiling in
    Arduino IDE for AVR seems to be use a more modern configuration... :confused:
    [AckermanControl.cpp, BrushedMotor.cpp, DifferentialControl.cpp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]
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2019-06-17 Remove duplicate code (#14)
    Fixes #13
    [SRF08.cpp]
2020-01-05 Specify library dependencies in library.properties (#19)
    Specifying the library dependencies in the depends
    Field of library.properties causes the Arduino Library
    Manager (Arduino IDE 1.8.10 and newer) to offer to
    install any missing dependencies during installation
    of this library. "arduino-cli lib install" will automatically
    Install the dependencies (arduino-cli 0.7.0 and newer).
2020-02-10 Remove duplicate code from initializer list (#20)
    Fixes #17
    [DistanceCar.cpp]
2020-02-12 Make Smartcar library compatible with ESP32
    To be able to compile the Smartcar library for ESP32
    we need to provide alternative implementations for:
    * analogWrite
    * Servo library
    To achieve this we use as submodules existing libraries
    that offer the missing functionality and have adjusted
    the implementation accordingly. The way it's done right
    now, i.e. with ifdef statements is perhaps not the best
    but it's good enough for now.
    [ArduinoRuntime.cpp, ServoMotor.hpp]
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2020-02-12 Fix Servo header inclusion
    As of Arduino IDE 1.8.11 a bug related to tracking
    the correct library is fixed, so now we can include
    the Servo.h again.
    [ServoMotor.hpp]
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2020-02-12 Remove std::bind since it is not solving the RAM issue
    [ArduinoRuntime.cpp, DistanceCar.ino, PidControllerMonitor.ino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]
2020-02-12 Remove error value return when Odometer not attached
    If an Odometer is not attached due to bad pin, then no good
    values will be received anyway and the user can check if this
    happened succesfully by calling the isAttached method.
2020-02-12 Fix clang-tidy warnings and run it on CI
    [DistanceCar.cpp, ServoMotor.cpp, ServoMotor.hpp]
2020-02-12 Fix getOffset returning unsigned division results on ESP32
    [GY50.cpp]
2020-02-12 Return signed int with getHeading
    Generally, unsigned seems to be creating more problems
    than providing disambiguity
    [GY50.cpp, automatedMovements.ino, rotateOnSpot.ino]
2020-02-12 Brake more smoothly to avoid excess power pull
    [DistanceCar.cpp]
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2020-02-14 Add smartcar platform PCBs
    [modules_board.brd, modules_board.sch, motor_board.brd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]
2020-02-14 Fix broken examples due to misformatting
    [HeadingCar.ino, manualControl.ino, shieldMotorsTest.ino]
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2020-05-28 Remove variable length array
    VLAs are not ISO C++ compliant and despite being supported
    by GCC, that may not be the case with other compilers.
    Fixes #22
    [SRF08.cpp]
2020-05-28 Add compiler flags and fix warnings
    [DifferentialControl.cpp, DistanceCar.cpp, GY50.cpp]
2020-05-28 Fix clang-9 compilation warnings
    [SRF08.cpp]
2020-06-07 Remove hardcoded arduino runtime injection
    The ArduinoRuntime was thus far injected by default in all
    classes that needed it. This was achieved with a small 'hack'
    which is now removed, in the name of consistency and object
    orientation. This will also make it slightly simpler to move
    to other platforms.
    As a consequence, this is a backwards incompatible change.
    [BrushedMotor.cpp, DistanceCar.cpp]
2020-06-07 Rename runtime variable to avoid clash in espressif sdk
    [DistanceCar.ino, FullSerialControl.ino]
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2020-11-15 Undo some fixes due to lack of support on 8bit AVR
    [DistanceCar.cpp]
2021-05-01 Fix ESP32 power supply line to 5V
    ESP32 was powered on via its VIN pin which based
    on the specs of the ESP32 DOIT devkit is supposed
    to handle up to 12V.
    This isn't actually the case and anything above 6V
    makes the regulator on the board overheat.
    Note that the 5V is actually the voltage coming from
    our own on-board regulator.
    [modules_board.brd, modules_board.sch]
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2022-03-19 Declare functions before usage
    Arduino IDE is fine with this, however when compiling
    on Windows within SMCE, this doesn't work.
    So let's start using more proper C++ and do things properly
    that work everywhere.
    [FullSerialControl.ino, SerialControlServoESC.ino, automatedMovements.ino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]
2022-03-19 Use brace initialization for Odometer constructors
    Let's use brace initialization for Odometer constructors not
    so much because it's more idiomatic, but mostly due to problems
    when compiling with SMCE on Windows
    [DistanceCar.ino, PidControllerMonitor.ino, SmartCar.ino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]
2023-03-12 Support dual motors
    Add support for motors connected on different pins but controlled
    in the same way.
    This is useful when we have two motor drivers and four
    different motors where the two motors on each side of the car are
    connected to the same driver but on different pins.
    Fixes rosmo-robot/smartcar_shield#1

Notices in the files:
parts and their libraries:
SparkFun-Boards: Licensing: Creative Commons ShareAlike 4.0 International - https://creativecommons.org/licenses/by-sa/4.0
